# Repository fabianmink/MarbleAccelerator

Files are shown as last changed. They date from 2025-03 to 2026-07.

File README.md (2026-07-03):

# Marble Accelerator
This project deals with the construction of various accelerators (coil guns) for metallic marbles. It might be used e.g. for the GraviTrax marble run (marble data: $m = 8.6 \mathrm{g}$, $d = 12.7 \mathrm{mm}$). It has been used in various student projects in electrical engineering bachelor's and master's programs in the IEM department at the THM Friedberg, e.g. [this one](https://www.youtube.com/watch?v=bSArWLXCZdo) 

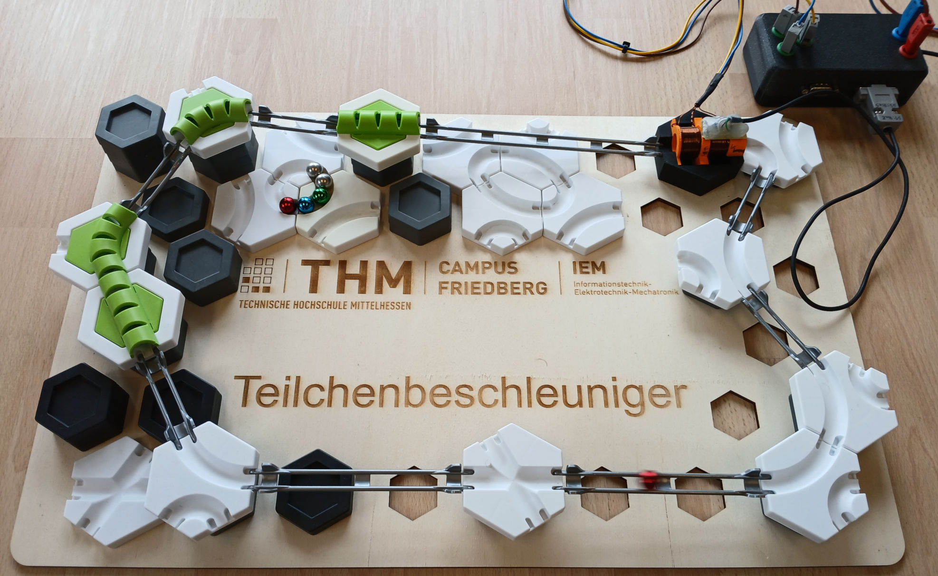
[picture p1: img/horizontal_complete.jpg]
Horizontal design complete
 

## Coilgun Designs

Coil winding cross sections are 15mm (coil length) x 7mm (inner radius 8mm, outer radius 15mm), leading to around 350 turns for 0.5mm wire diameter which results in an inductance of approximately 1mH.

### Horizontal coil design with two coils
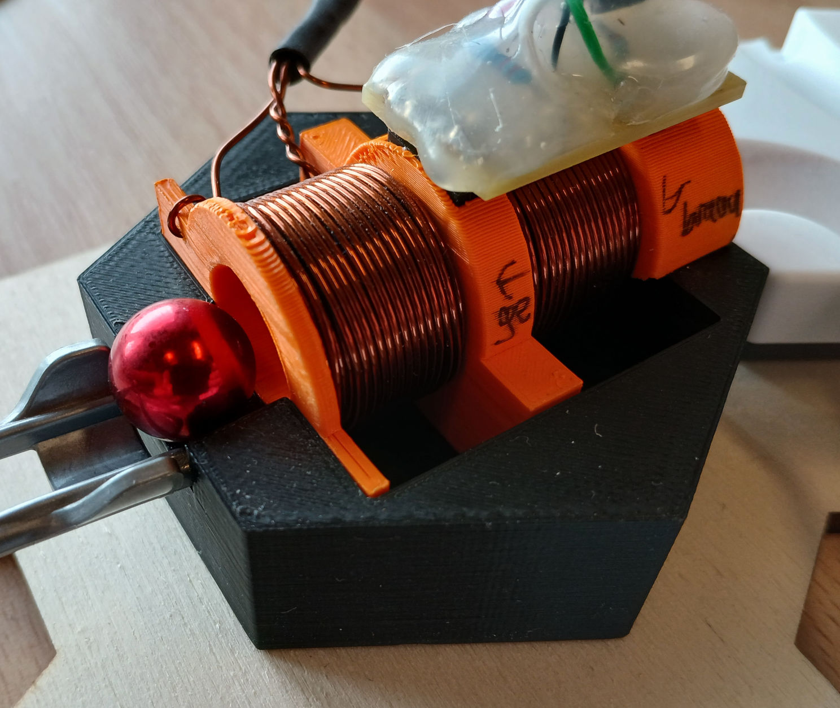
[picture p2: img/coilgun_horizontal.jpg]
Horizontal coil design


Horizontal CAD design (base and tube parts)

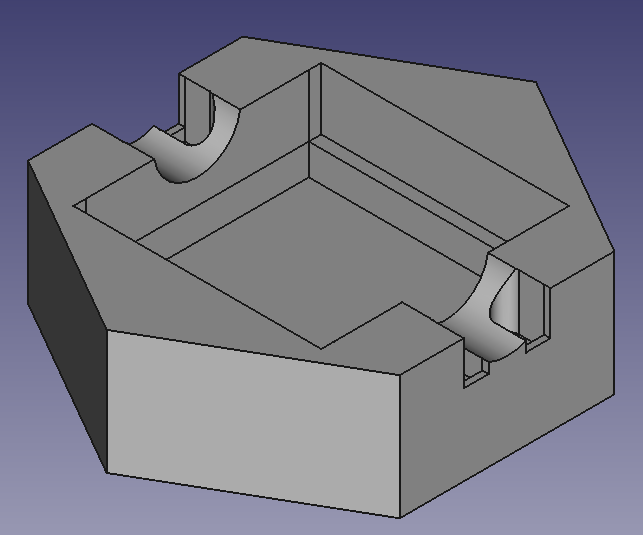
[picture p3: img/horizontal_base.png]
horizontal design base
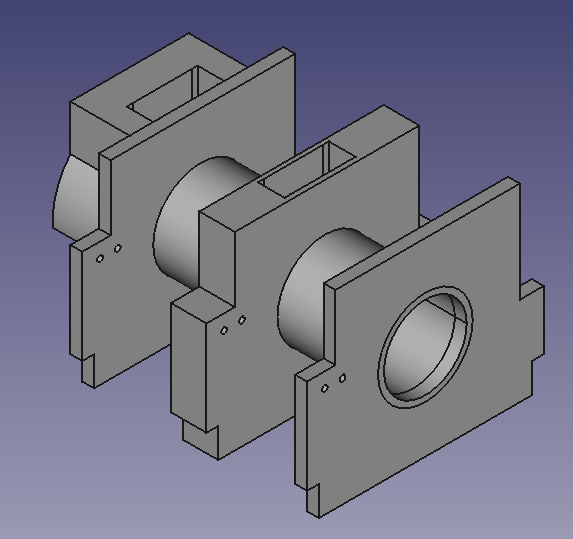
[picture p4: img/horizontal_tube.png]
horizontal design tube
 

The design is intended to be used with EVERLIGHT ITR9904 optical sensor for marble detection.

### Vertical coil design (single coil)

Vertical CAD design (base part and output)

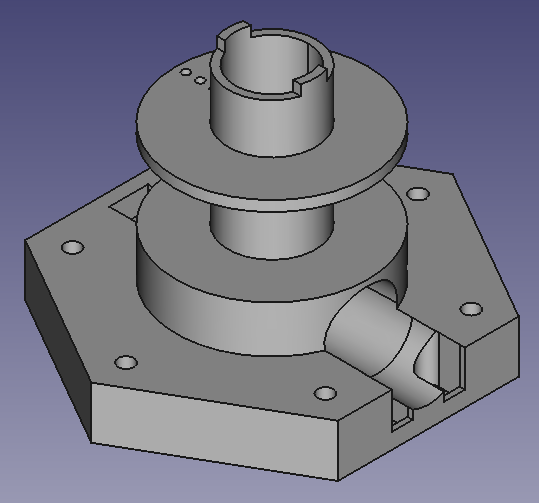
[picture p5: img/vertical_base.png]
vertical design base
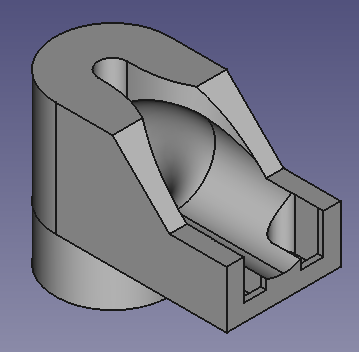
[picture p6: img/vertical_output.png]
vertical output
  

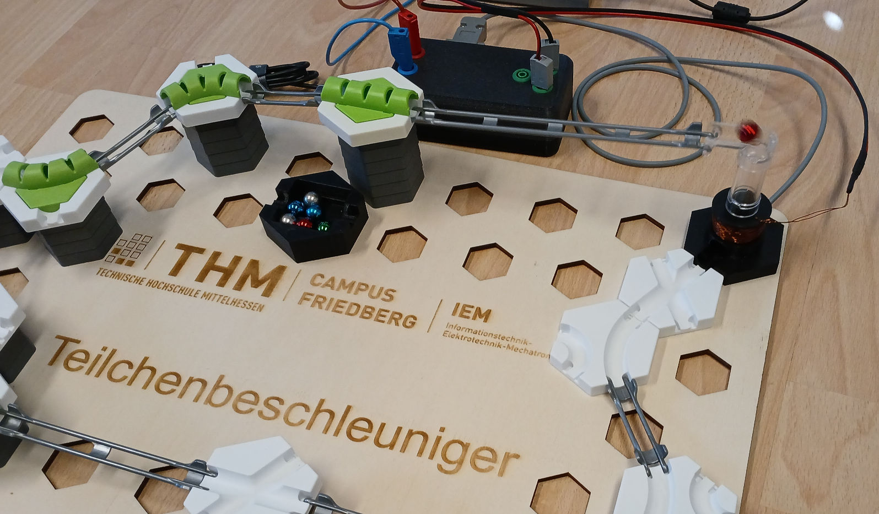
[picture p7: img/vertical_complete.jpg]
vertical whole marble track


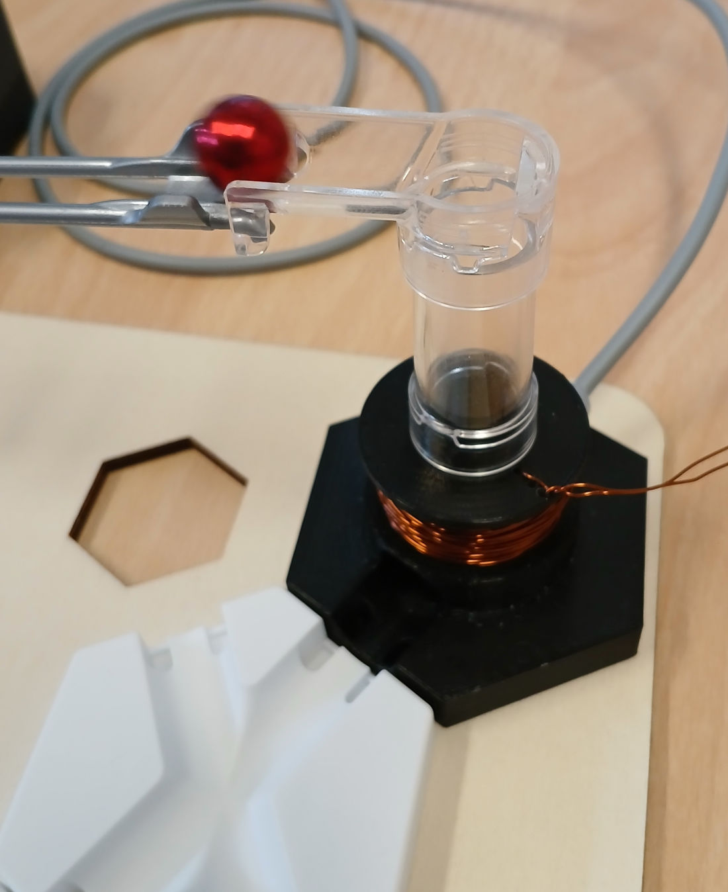
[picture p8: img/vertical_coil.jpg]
vertical design accelerator coil


The design is intended to be used with Vishay CNY70 optical sensor for marble detection.

The advantage of the vertical design is that the marble is at a defined state (no movement, $v_\mathrm{z} = 0$) at the beginning. This makes the accelerator parameters easier to tune, as the current level and duration of the current pulse are always the same.

## Coil winding
For an operating voltage of 24V, suitable wire diameters are in the range of 0.5mm ... 0.75mm.

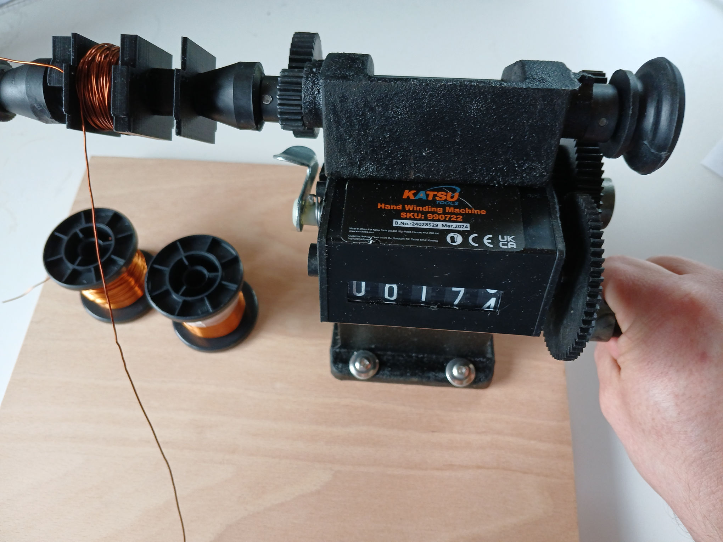
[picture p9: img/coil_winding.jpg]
coil winding machine


## FEM Simulation (FEMM)

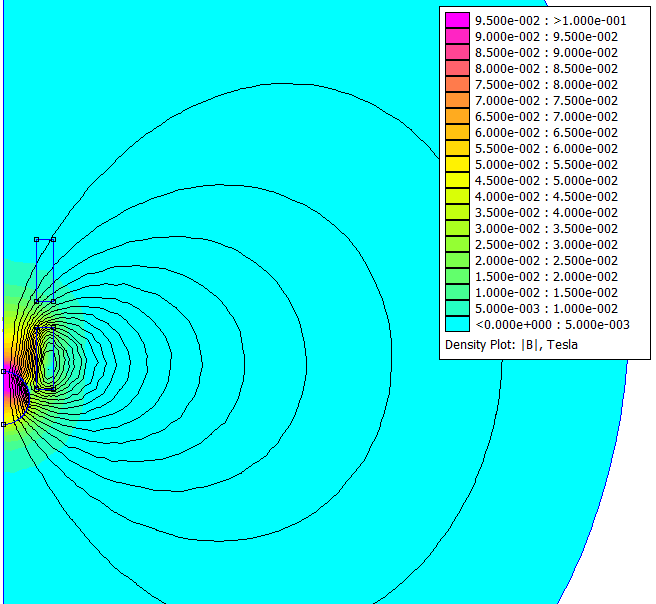
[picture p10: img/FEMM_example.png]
FEM Simulation


## Fitting of FEM results

The fit is based on the following coenergy equation:

- Co-Energy: $E_{\mathrm{Co}} = \frac{1}{2} \cdot L_\mathrm{min} \cdot I^2 \cdot \left[ 1 + d \cdot \exp \left( -0.5 \cdot \left(\frac{z - z_0}{z_\mathrm{s}}\right)^2 \right) \right]$

i.e.:

- z-Direction Force: $F_\mathrm{z} = \frac{\partial E_{\mathrm{Co}}}{\partial z} = - \frac{1}{2}  \cdot L_\mathrm{min} \cdot I^2 \cdot \left[ d \cdot \exp \left( -0.5 \cdot \left( \frac{z - z_0}{z_\mathrm{s}} \right)^2 \right) \right] \cdot \frac{z - z_0}{z^2_\mathrm{s}}$

- Flux Linkage: $\Psi = \frac{\partial E_{\mathrm{Co}}}{\partial I} = L_\mathrm{min} \cdot I \cdot \left[ 1 + d \cdot \exp \left( -0.5 \cdot \left( \frac{z - z_0}{z_\mathrm{s}} \right)^2 \right) \right]$

- Inductance: $L = \frac{\partial \Psi}{\partial I} = \frac{\partial^2 E_{\mathrm{Co}}}{\partial I^2} = L_\mathrm{min} \cdot \left[ 1 + d \cdot \exp \left( -0.5 \cdot \left( \frac{z - z_0}{z_\mathrm{s}} \right)^2 \right) \right]$

- Flux derivative: $\frac{\partial \Psi}{\partial z} = \frac{\partial^2 E_{\mathrm{Co}}}{\partial I \partial z} = - L_\mathrm{min} \cdot I \cdot \left[ d \cdot \exp \left( -0.5 \cdot \left( \frac{z - z_0}{z_\mathrm{s}} \right)^2 \right) \right] \cdot \frac{z - z_0}{z^2_\mathrm{s}}$ (needed for induced voltage calculation)

- Maximum force for given current occurs at the inflection points of $E_{\mathrm{Co}}$, i.e. at $z = z_0 \pm z_\mathrm{s}$: $F_\mathrm{z,max} \left( I \right)= \frac{1}{2}  \cdot L_\mathrm{min} \cdot I^2 \cdot d \cdot \exp \left( -0.5 \right) \cdot \frac{1}{z_\mathrm{s}}$

Resulting examplary fitted force:

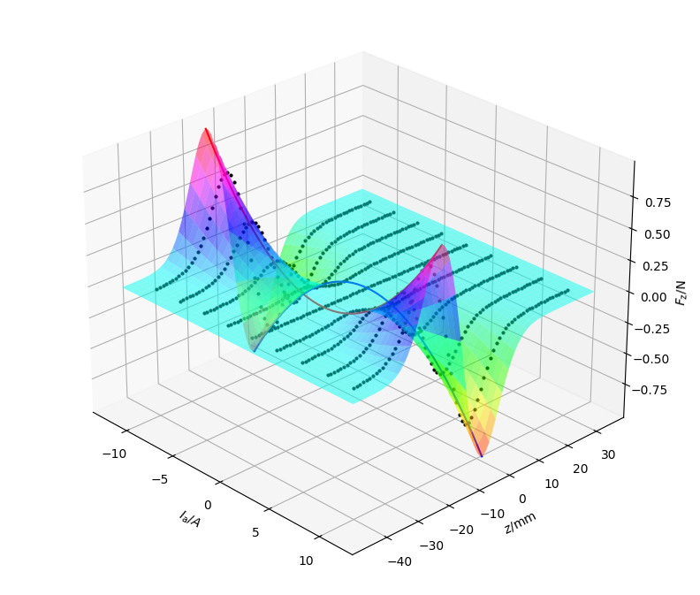
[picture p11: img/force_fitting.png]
Force Fit


## Dynamic System Simulation Model

The dynamic simulation implements the following equations:

- Velocity (z-direction): $\dot{v} = \frac{1}{m} \cdot F_\mathrm{z}$
- z-Position: $\dot{z} = v$
- Force calculation: $F_\mathrm{z} = F_\mathrm{z}\left(I, z\right)$ (see equation in chapter above)
- Coil current: $\dot{I} = \frac{1}{L \left(I, z\right) } \cdot \left[ u - R \cdot I - u_\mathrm{ind} \right]$
- Induced voltage: $u_\mathrm{ind} = \frac{\partial \Psi}{\partial z} \cdot v$

Model:

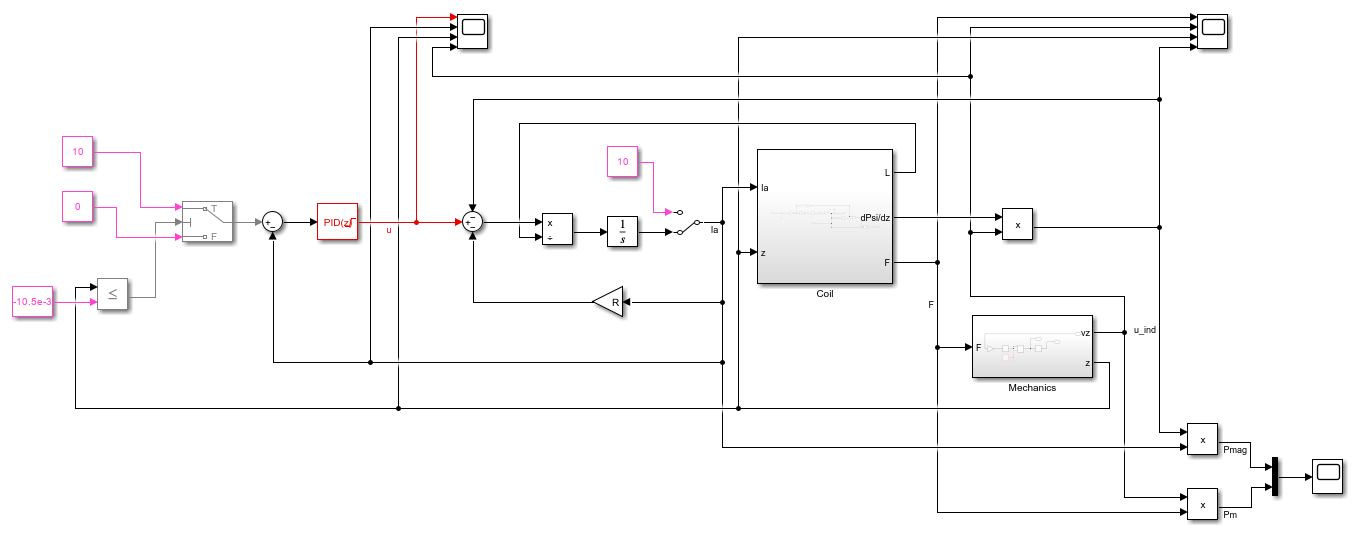
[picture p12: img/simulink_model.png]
System Simulation


Coil electromagnetic subsystem:

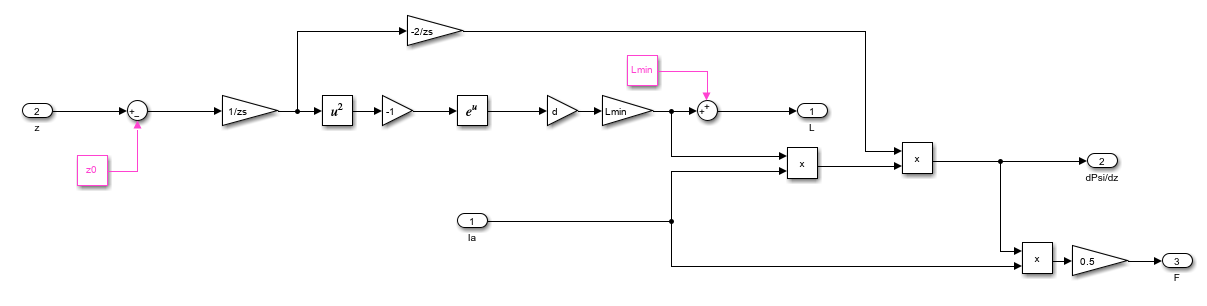
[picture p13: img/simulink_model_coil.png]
Model of coil electromagnetic system


## Power Electronics / Software

The software is designed for STM's B-G431B-ESC1 (Discovery kit with STM32G431CB MCU); it also includes the neccessary power MOSFETs. The supply voltage is 24V. An external capacitor of approximately 20mF is recommended in order to provide the high pulsed currents of 10..20A for durations of a few 10ms.

### Boost Converter

In case the coil should be battery-powered (e.g. from 3x AA alkaline cells / 4.5V), the boost converter board can be used.

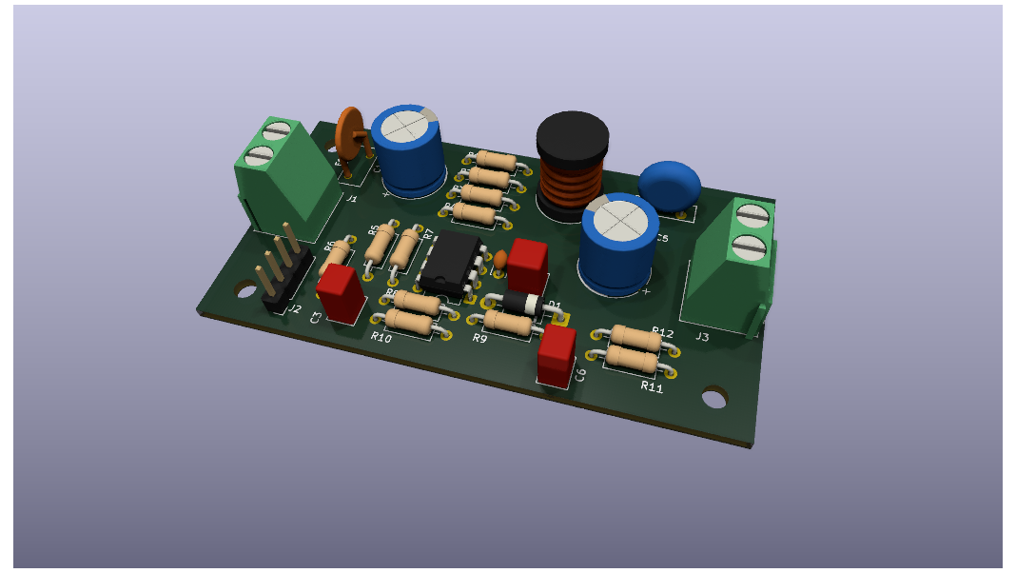
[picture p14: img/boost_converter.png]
Boost Converter Board


### Hi-Side Switch

Can be used to power the coil.

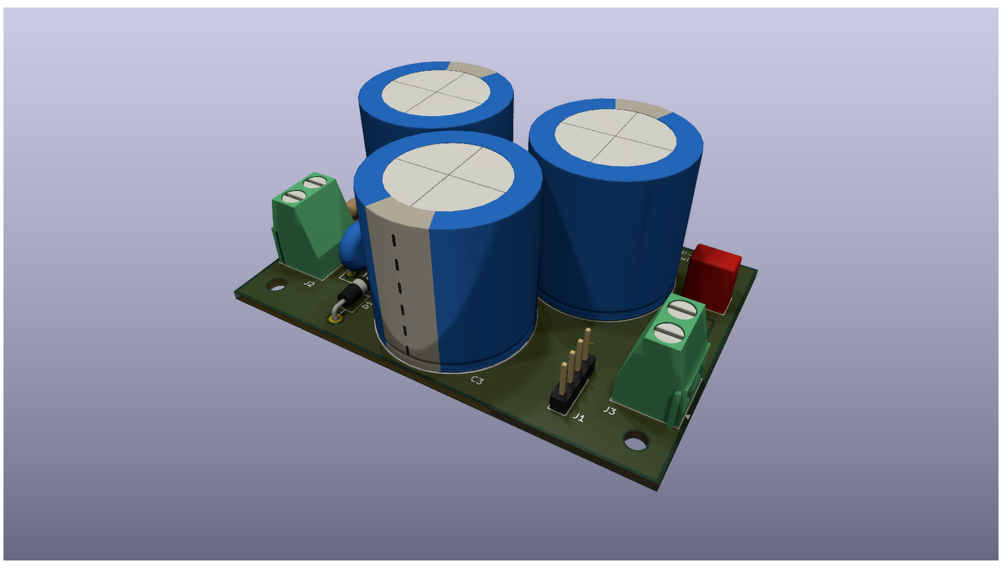
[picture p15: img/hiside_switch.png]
Hi-Side Switch Board


## Simlar projects

- [lincoln1clarke (Instructables) - Electromagnetic Marble Accelerator for Gravitrax](https://www.instructables.com/Electromagnetic-Marble-Accelerator-for-Gravitrax/)
- [HyperspacePirate (Thingiverse) - Electromagnetic Accelerator](https://www.thingiverse.com/thing:4918703)
- [William Le - Perpetual Marble Machine](https://lovelywings.store/)

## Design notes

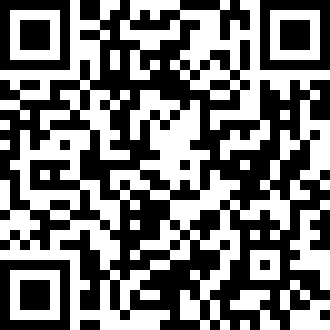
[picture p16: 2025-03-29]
img/MarbleAccelerator.png

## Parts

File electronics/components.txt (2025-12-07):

Input current limitation
Preferred Input voltage U = 3V / Ri = 0.3Ohm
(2x Alkaline)
https://de.wikipedia.org/wiki/Alkali-Mangan-Zelle
Gemessener Kurzschlussstrom (1x Aldi-Zelle AA): 7.5A (mit Messleitungen) -> Ri ~~ 0.15 .. 0.2 Ohm kommt hin
Eingangsstrom auf 1A begrenzen (PTC-Sicherung)
-> 3W
Bspw. Kosmos 3V-Batteriemodule 2xAA PTC "X30 UF110" vermutl. 30V, 1.1A (Reichelt "PTC FRU11030F" (Eska) ), begrenzen auf ca. 6A messtechnisch ermittelt (passt zu Datenblattangabe 50mOhm...170mOhm Innenwiderstand)
Denkbare Typen:
Reichelt PTC FRU09030F  (30V, 0.9A)
Reichelt PTC FRU11030F  (30V, 1.1A)
Reichelt PTC FRX05060F  (60V, 500mA)
Reichelt PTC FRX11060F  (60V, 1.1A)

Power Switches
BTS 6163 D Smart Highside Power Switch

Storage Capacitor
Cstor ≈ 20mF
e.g. 
2x Reichelt BSN 10.000/25     Becher-Elko, radial, 10 mF, 25 
1x Reichelt BSN 22.000/40     Becher-Elko, radial, 22 mF, 40 

PTC, for Charging Cstor
e.g.
Reichelt  EPC B59990-C80      Infineon PTC Widerstand, 55 Ohm, 80 V, 80°C 

DC-DC converter
MC34063A
1N5819
Rsc = 2W, ≈ 0.2Ohm
L ≈ 170uH
Cin = 100uF, low ESR
Cout = 330uF, low ESR

Reflective Optical Sensor
CNY 70
ELI TR9904

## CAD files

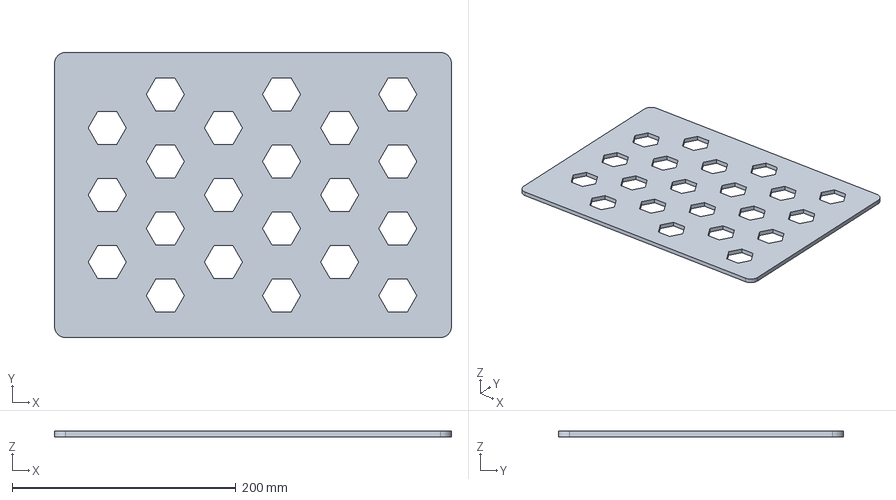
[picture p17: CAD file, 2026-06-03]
cad/Baseplate_35cmx25cm_variableCell.FCStd
355.0 x 255.0 x 5.00 mm

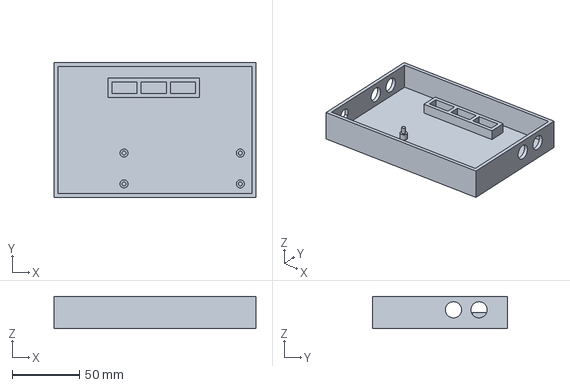
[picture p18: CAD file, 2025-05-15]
cad/controller/baseplate.FCStd
150.0 x 100.0 x 24.0 mm

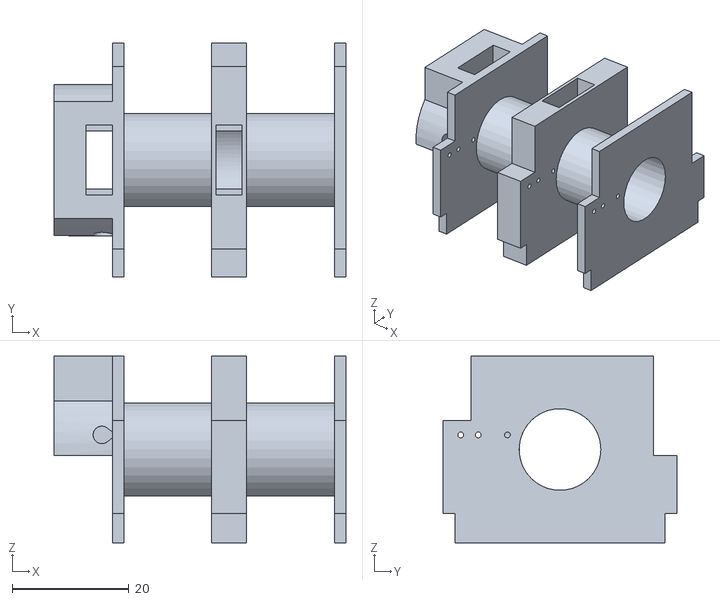
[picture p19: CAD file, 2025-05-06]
cad/horizontal/tube-Body.stl
50.0 x 40.0 x 32.0

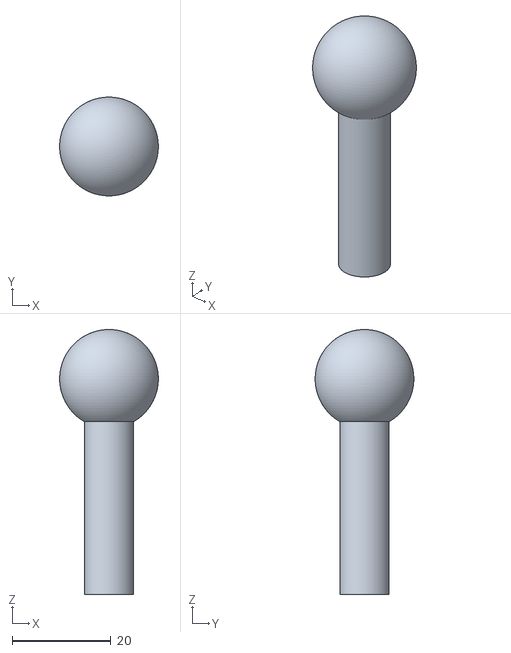
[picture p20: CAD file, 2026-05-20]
cad/magnet/magnetHolder-Body.stl
20.0 x 20.0 x 53.7

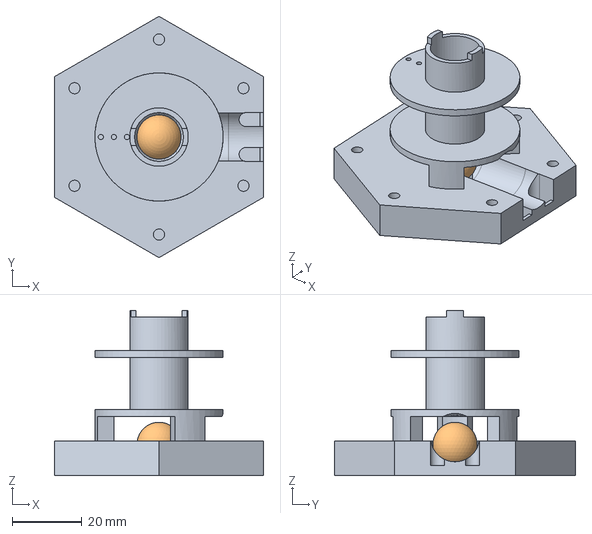
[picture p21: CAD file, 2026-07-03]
cad/vertical/base_open.FCStd
60.0 x 69.3 x 47.5 mm
Marble

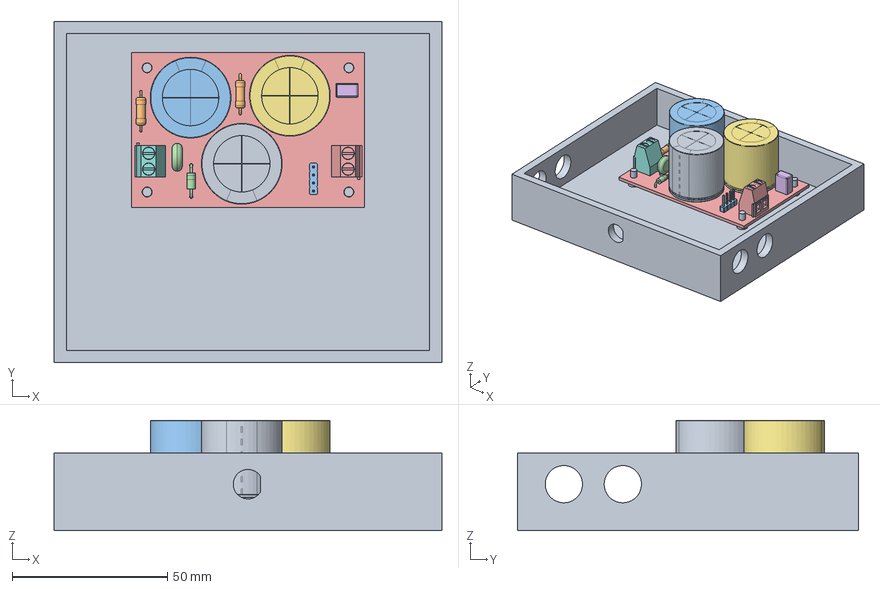
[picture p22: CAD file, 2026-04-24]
electronics/housing/board_carrier_SwitchOnly.FCStd
125.0 x 110.0 x 35.6 mm
BoardCarrier
R_Axial_DIN0309_L9.0mm_D3.2mm_P12.70mm_Horizontal
PinHeader_1x04_P2.54mm_Vertical
D_DO-41_SOD81_P10.16mm_Horizontal
TerminalBlock_Phoenix_MKDS-1,5-2-5.08_1x02_P5.08mm_Horizontal
C_Rect_L7.2mm_W4.5mm_P5.00mm_FKS2_FKP2_MKS2_MKP2
CP_Radial_D26.0mm_P10.00mm_SnapIn
TerminalBlock_Phoenix_MKDS-1,5-2-5.08_1x02_P5.08mm_Horizontal001
CP_Radial_D26.0mm_P10.00mm_SnapIn001
R_Axial_DIN0309_L9.0mm_D3.2mm_P12.70mm_Horizontal001
CP_Radial_D26.0mm_P10.00mm_SnapIn002
RV_Disc_D9mm_W3.3mm_P5mm
R_0805_2012Metric
C_0805_2012Metric
R_0805_2012Metric001
R_0805_2012Metric002
C_0805_2012Metric001
SOT-23
R_0805_2012Metric003
hiside_switch 1.19.1
hiside_switch 1.19.002
hiside_switch 1.19.003
hiside_switch 1.19.004
hiside_switch 1.19.005
hiside_switch 1.19.006
hiside_switch 1.19.007
R_0805_2012Metric004
R_0805_2012Metric005
hiside_switch_PCB

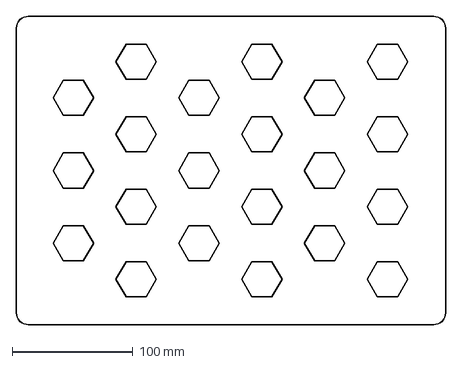
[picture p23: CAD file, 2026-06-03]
cad/Baseplate_35cmx25cm-BodySketch_Baseplate.dxf
355.0 x 255.0 mm

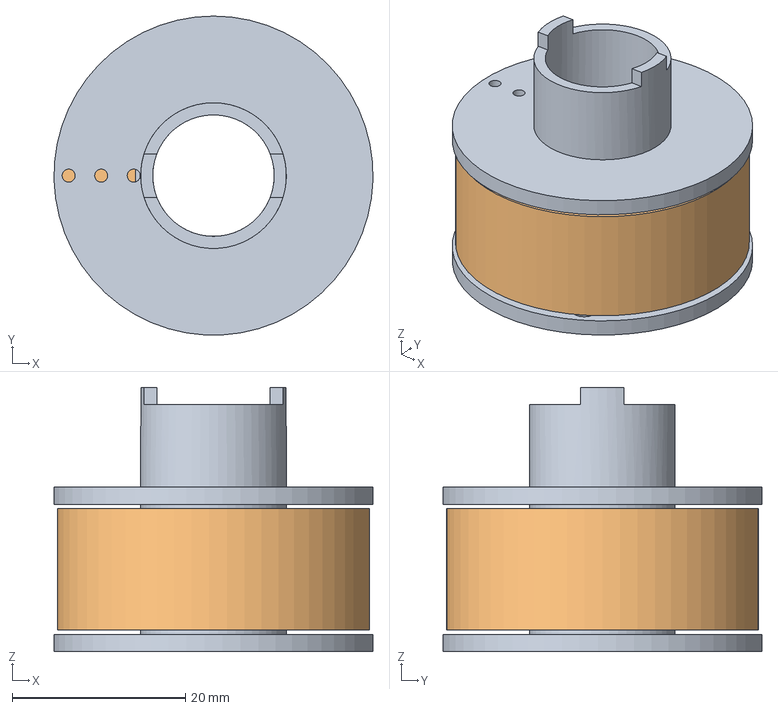
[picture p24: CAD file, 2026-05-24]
cad/vertical/base_open_coil.FCStd
36.8 x 36.8 x 30.5 mm
Body_Winding

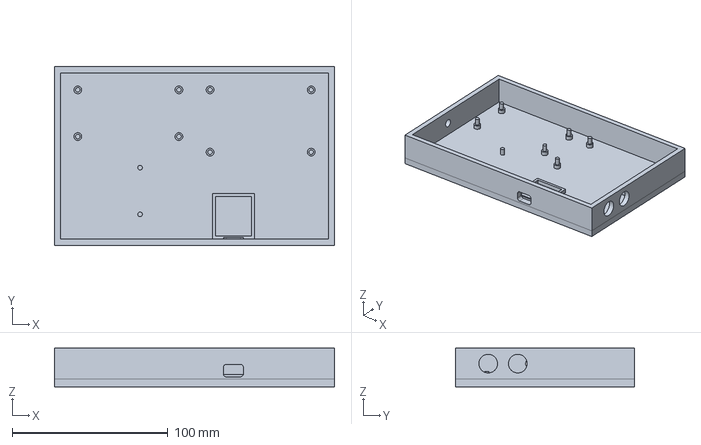
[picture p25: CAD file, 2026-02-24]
electronics/housing/board_carrier.FCStd
180.0 x 115.0 x 25.0 mm

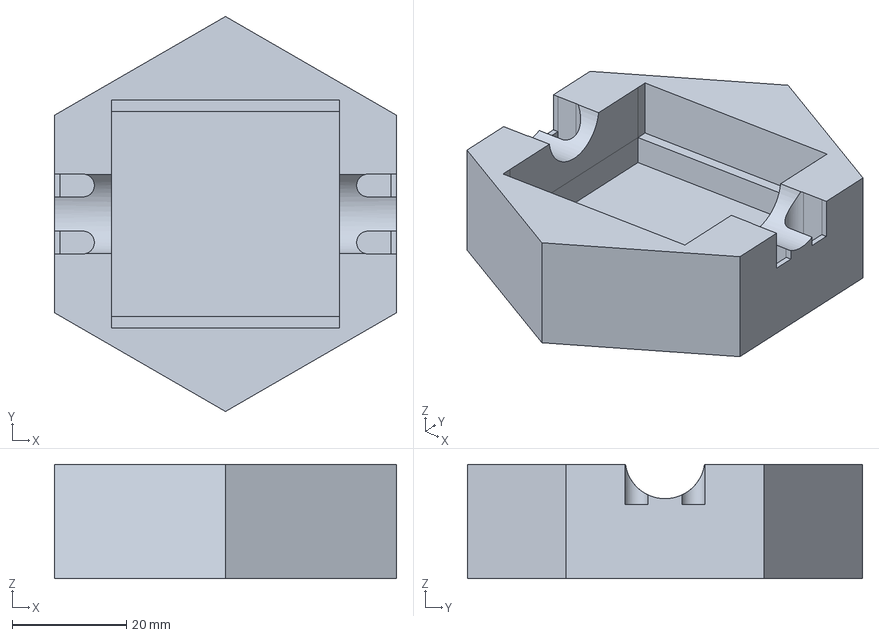
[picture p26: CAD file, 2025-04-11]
cad/horizontal/base.FCStd
60.0 x 69.3 x 20.0 mm

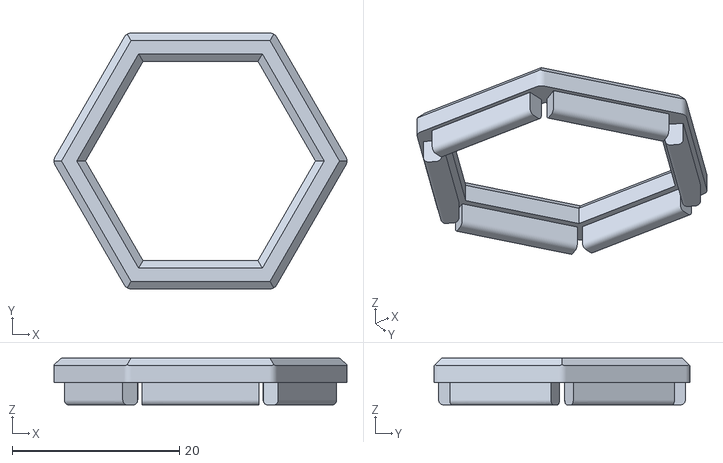
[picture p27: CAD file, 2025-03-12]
cad/ring.stl
35.0 x 30.6 x 5.60

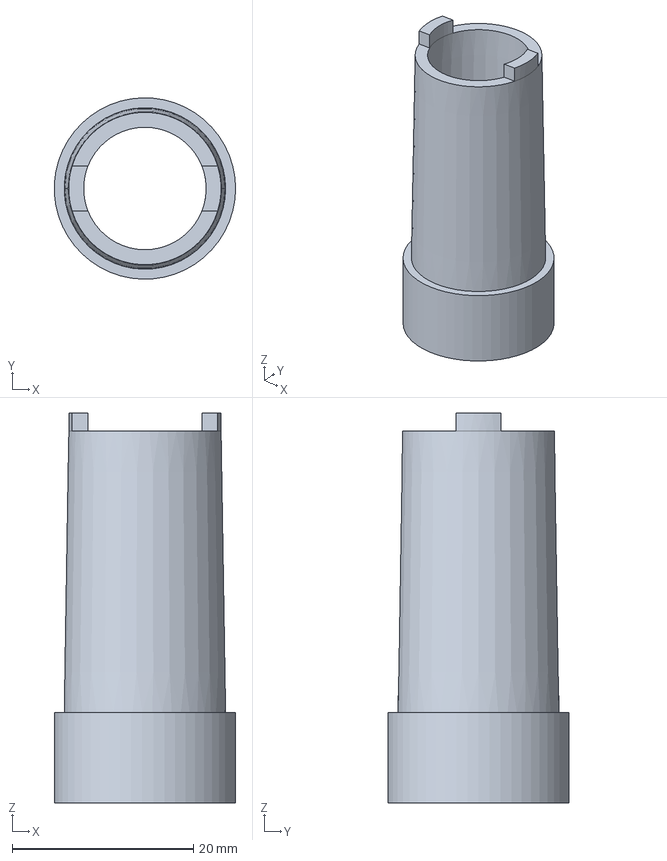
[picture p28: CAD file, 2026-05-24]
cad/vertical/extensionTube.FCStd
20.0 x 20.0 x 43.0 mm

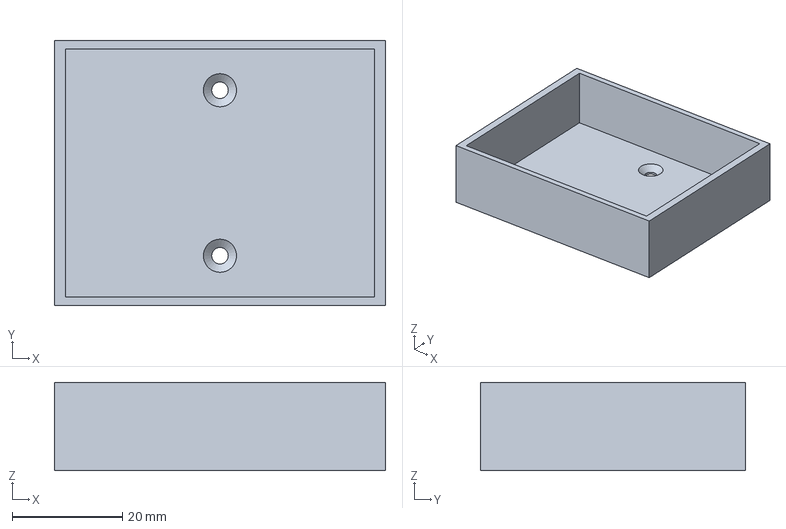
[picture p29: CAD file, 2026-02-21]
electronics/housing/batteryHolder.FCStd
60.0 x 48.0 x 16.0 mm

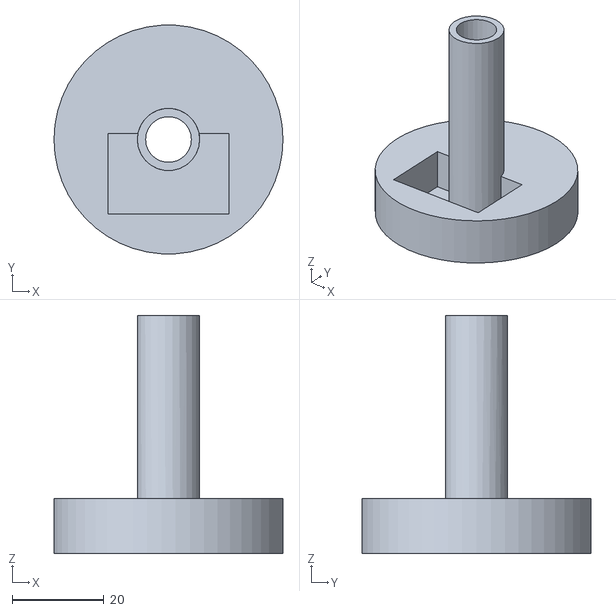
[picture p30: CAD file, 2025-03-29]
cad/horizontal/winding_assistant-Body.stl
50.0 x 49.9 x 52.0

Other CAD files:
electronics/housing/electronicsAssembly.FCStd
cad/controller/baseplate-Body.stl
cad/horizontal/tube.FCStd
cad/magnet/magnetHolder.FCStd
cad/horizontal/base-Body.stl
cad/horizontal/winding_assistant.FCStd
cad/vertical/Pin-Body.stl
cad/vertical/Pin.FCStd
cad/vertical/base-Body.stl
cad/vertical/base.FCStd
cad/vertical/base_open-Body.stl
cad/vertical/base_open_base-Body.stl
cad/vertical/base_open_base.FCStd
cad/vertical/base_open_coil-Body.stl
cad/vertical/base_open_coil_noTop-Body.stl
cad/vertical/base_open_coil_noTop.FCStd
cad/vertical/extensionTube-Body.stl
cad/vertical/extensionTube_70mm-Body.stl
cad/vertical/outputCatcher-Body.stl
cad/vertical/outputCatcher.FCStd
cad/vertical/outputCatcherFilled-Body_Catcher.stl
cad/vertical/outputCatcherFilled-Body_Plate.stl
cad/vertical/outputCatcherFilled.FCStd
cad/vertical/outputTube-Body.stl
cad/vertical/outputTube.FCStd
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

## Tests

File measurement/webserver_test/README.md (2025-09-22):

# Webserver-Test

This is test application framework for displaying measurements on a webpage using uvicorn webserver / plotly. Code was partly developed in CaseStudy Project in Summer 2025.

Currently, it does not work together with the accelerator firmware for the STM32 controller of this project.

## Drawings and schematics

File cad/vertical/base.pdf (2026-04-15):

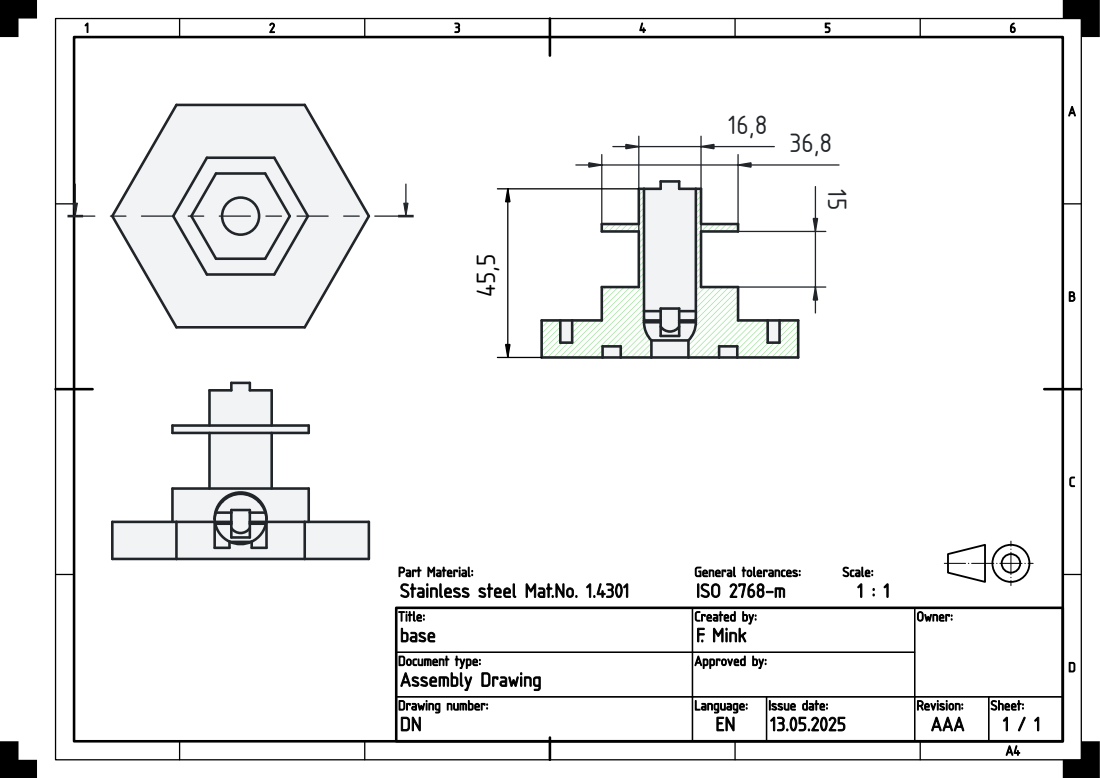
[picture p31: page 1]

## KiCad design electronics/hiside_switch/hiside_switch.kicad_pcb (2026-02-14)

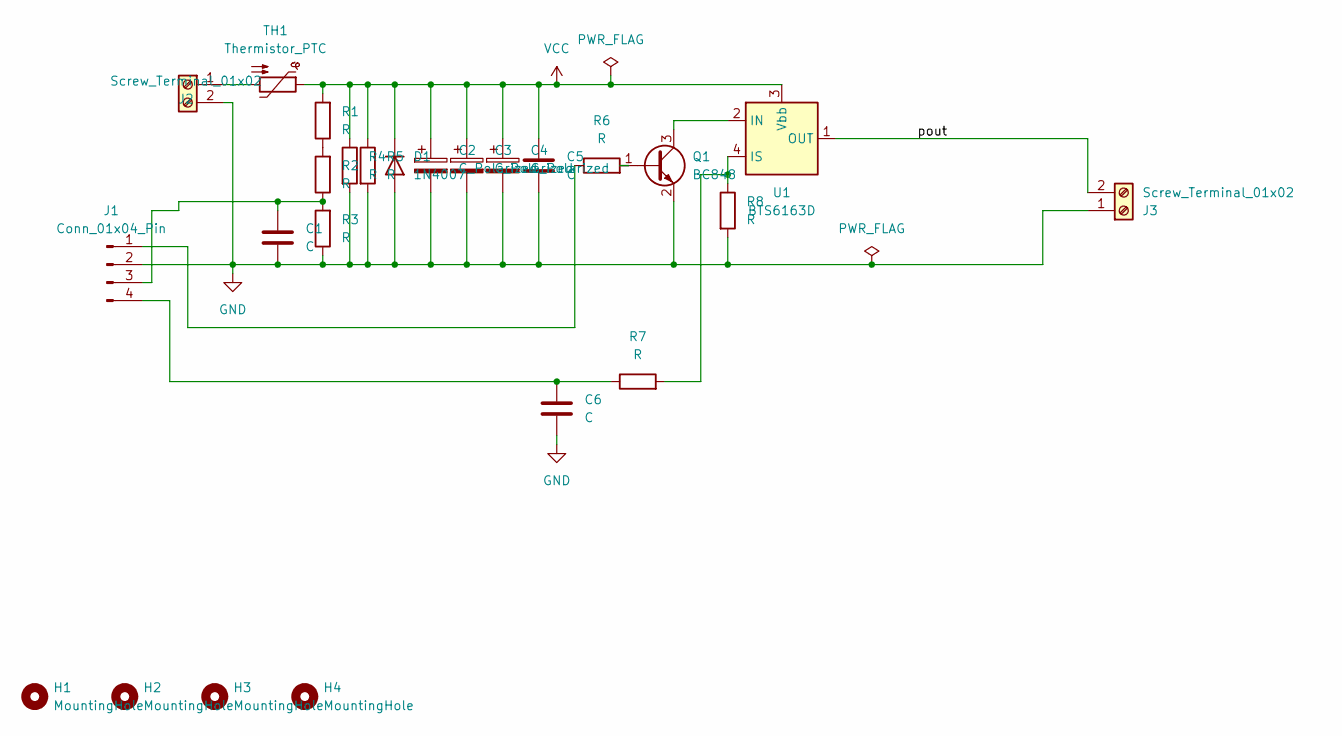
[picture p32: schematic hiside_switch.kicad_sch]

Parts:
C1, C6: C; C_0805_2012Metric_Pad1.18x1.45mm_HandSolder
C2, C3, C4: C_Polarized; CP_Radial_D26.0mm_P10.00mm_SnapIn
C5: C; C_Rect_L7.2mm_W4.5mm_P5.00mm_FKS2_FKP2_MKS2_MKP2
D1: 1N4007; D_DO-41_SOD81_P10.16mm_Horizontal
H1, H2, H3, H4: MountingHole; MountingHole_3.2mm_M3
J1: Conn_01x04_Pin; PinHeader_1x04_P2.54mm_Vertical
J2, J3: Screw_Terminal_01x02; TerminalBlock_Phoenix_MKDS-1,5-2-5.08_1x02_P5.08mm_Horizont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
Q1: BC848; SOT-23
R1, R2, R3, R6, R7, R8: R; R_0805_2012Metric_Pad1.20x1.40mm_HandSolder
R4, R5: R; R_Axial_DIN0309_L9.0mm_D3.2mm_P12.70mm_Horizontal
TH1: Thermistor_PTC; RV_Disc_D9mm_W3.3mm_P5mm
U1: BTS6163D; TO-252-4

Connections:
/pout: J3.2, U1.1 (OUT), U1.5 (OUT)
GND: C1.2, C2.2, C3.2, C4.2, C5.2, C6.2, D1.2 (A), J1.2, J2.2, J3.1, Q1.2 (E), R3.1, R4.2, R5.2, R8.2
unnamed: J1.1, R6.1
unnamed: C1.1, J1.3, R2.1, R3.2
unnamed: C6.1, J1.4, R7.1
unnamed: J2.1, TH1.2
unnamed: Q1.1 (B), R6.2
unnamed: Q1.3 (C), U1.2 (IN)
unnamed: R1.1, R2.2
unnamed: R7.2, R8.1, U1.4 (IS)
VCC: C2.1, C3.1, C4.1, C5.1, D1.1 (K), R1.2, R4.1, R5.1, TH1.1, U1.3 (Vbb)

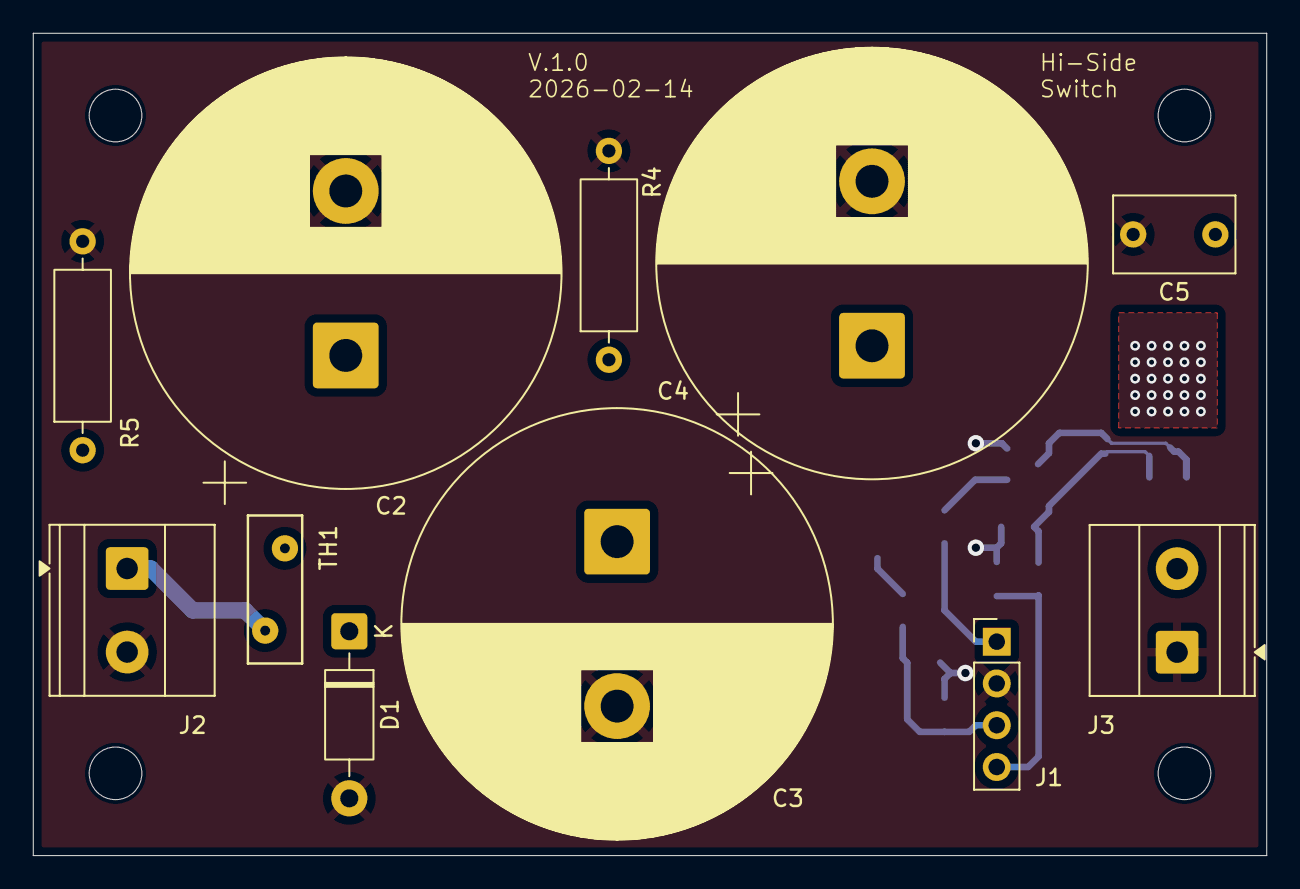
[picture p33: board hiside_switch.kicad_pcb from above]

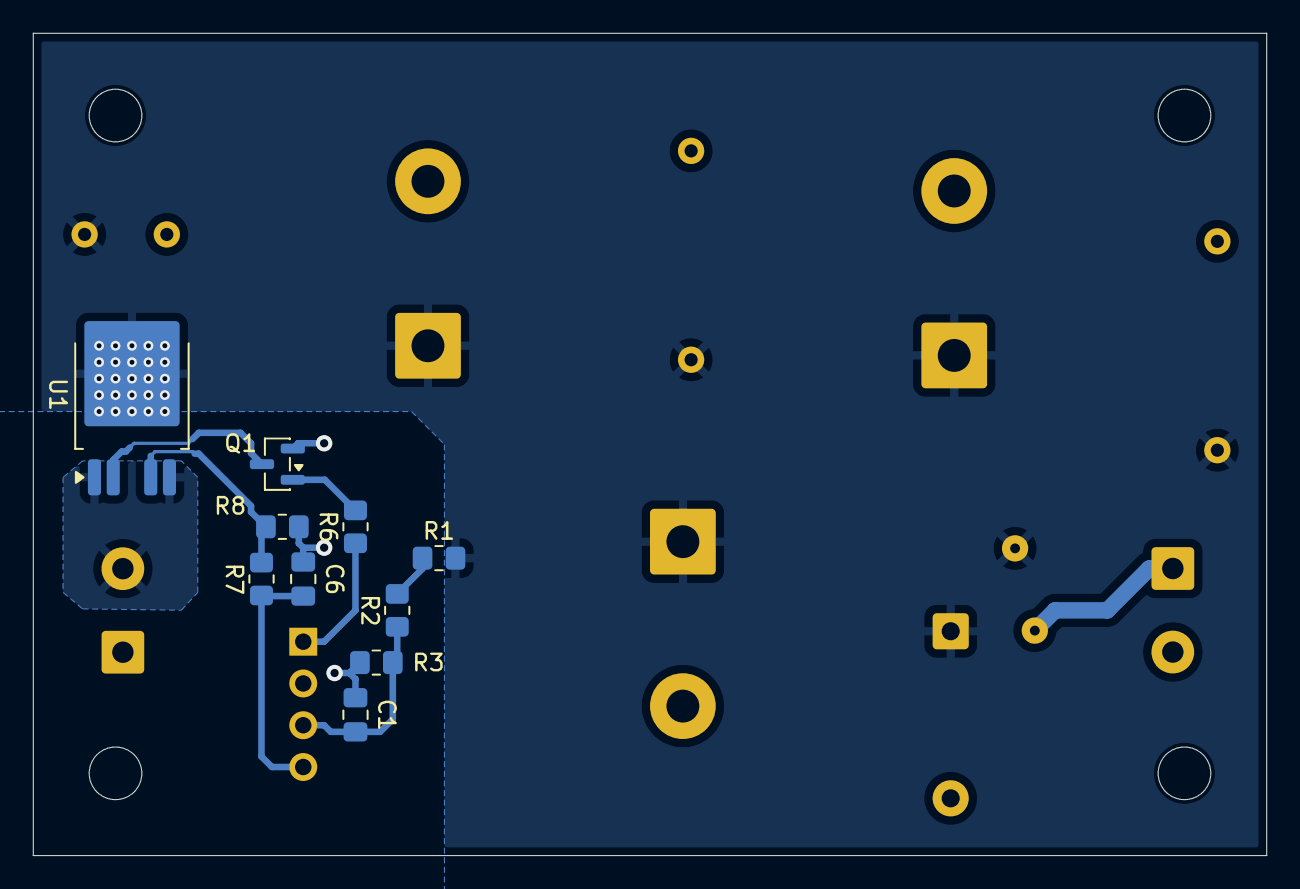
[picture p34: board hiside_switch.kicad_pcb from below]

Board: 2 copper layers, 75.0 x 50.0 mm, 25 parts (10 on the bottom side), 11 nets.

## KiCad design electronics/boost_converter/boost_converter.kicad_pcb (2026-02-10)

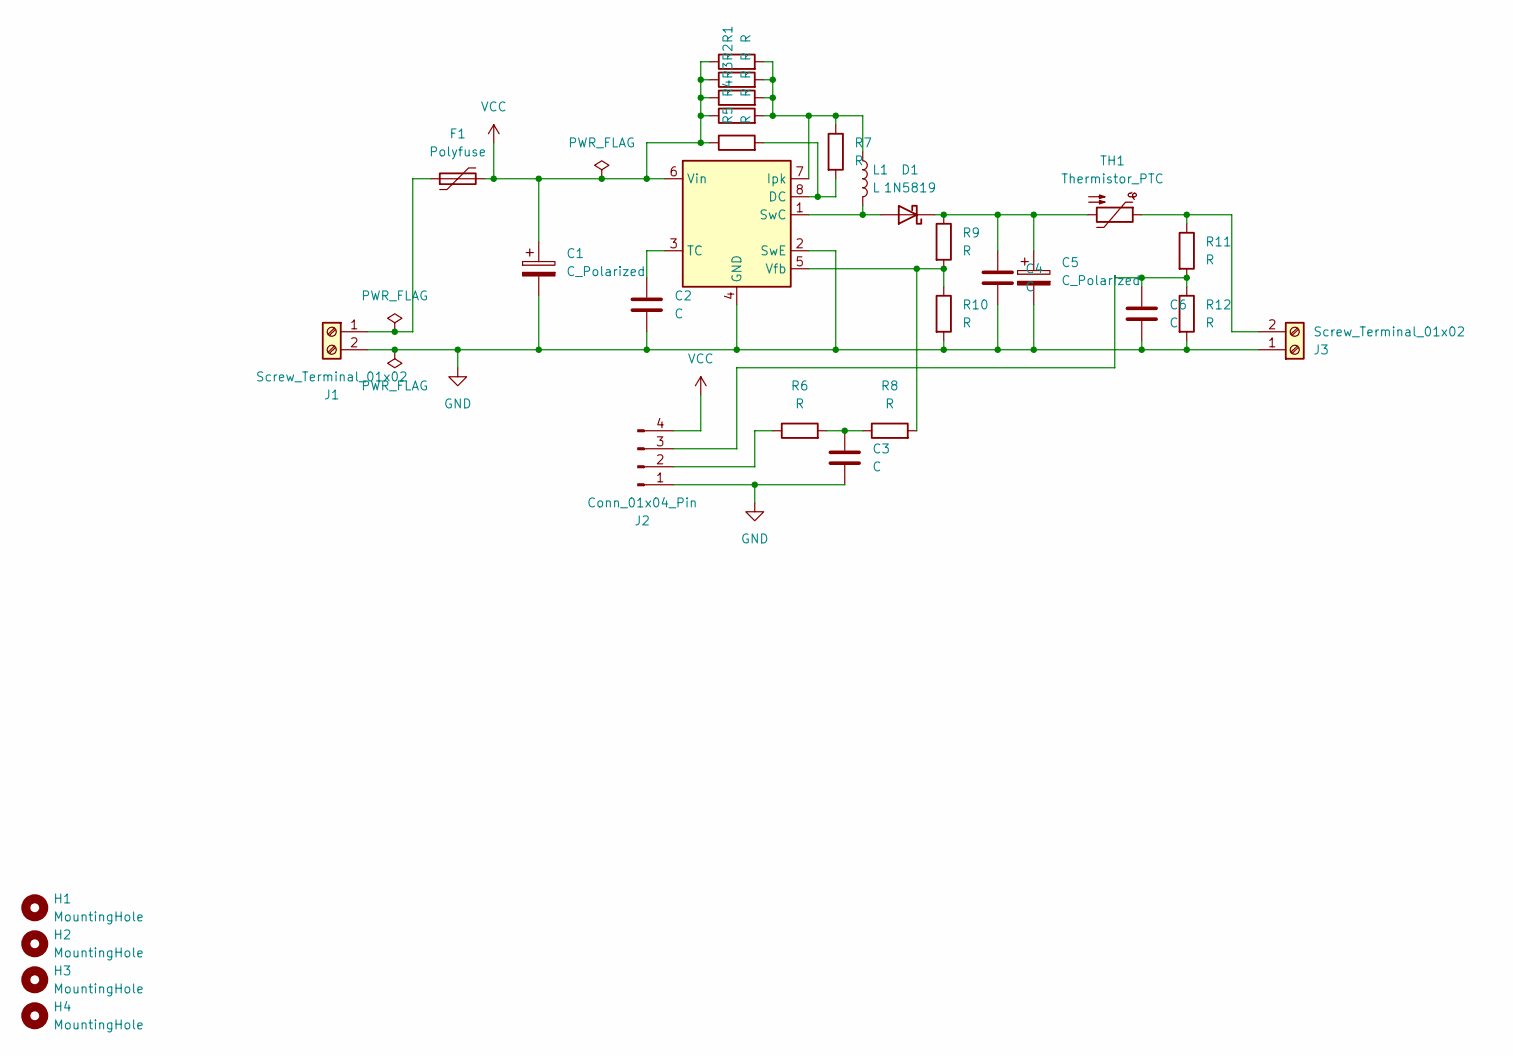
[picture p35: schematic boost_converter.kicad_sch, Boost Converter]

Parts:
C1: C_Polarized; CP_Radial_D10.0mm_P2.50mm_P5.00mm
C2: C; C_Disc_D3.0mm_W2.0mm_P2.50mm
C3, C6: C; C_Rect_L4.6mm_W3.8mm_P2.50mm_MKS02_FKP02
C4: C; C_Rect_L4.6mm_W4.6mm_P2.50mm_MKS02_FKP02
C5: C_Polarized; CP_Radial_D10.0mm_P5.00mm_P7.50mm
D1: 1N5819; D_DO-41_SOD81_P10.16mm_Horizontal
F1: Polyfuse; Fuse_BelFuse_0ZRE0005FF_L8.3mm_W3.8mm
H1, H2, H3, H4: MountingHole; MountingHole_3.2mm_M3
J1, J3: Screw_Terminal_01x02; TerminalBlock_Phoenix_MKDS-1,5-2-5.08_1x02_P5.08mm_Horizont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
J2: Conn_01x04_Pin; PinHeader_1x04_P2.54mm_Vertical
L1: L; L_Radial_D10.0mm_P5.00mm_Fastron_07P
R1, R2, R3, R4, R5, R6, R7, R8, R9, R10, R11, R12: R; R_Axial_DIN0207_L6.3mm_D2.5mm_P10.16mm_Horizontal
TH1: Thermistor_PTC; RV_Disc_D9mm_W3.3mm_P5mm
U1: MC34063AP; DIP-8_W7.62mm

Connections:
GND: C1.2, C2.2, C3.2, C4.2, C5.2, C6.2, J1.2, J2.1, J3.1, R10.2, R12.2, U1.2 (SwE), U1.4 (GND)
unnamed: C3.1, R6.2, R8.1
unnamed: D1.2 (A), L1.2, U1.1 (SwC)
unnamed: C4.1, C5.1, D1.1 (K), R9.1, TH1.2
unnamed: F1.1, J1.1
unnamed: J2.2, R6.1
unnamed: C6.1, J2.3, R11.2, R12.1
unnamed: J3.2, R11.1, TH1.1
unnamed: R5.2, R7.2, U1.8 (DC)
unnamed: L1.1, R1.2, R2.2, R3.2, R4.2, R7.1, U1.7 (Ipk)
unnamed: C2.1, U1.3 (TC)
unnamed: R8.2, R9.2, R10.1, U1.5 (Vfb)
VCC: C1.1, F1.2, J2.4, R1.1, R2.1, R3.1, R4.1, R5.1, U1.6 (Vin)

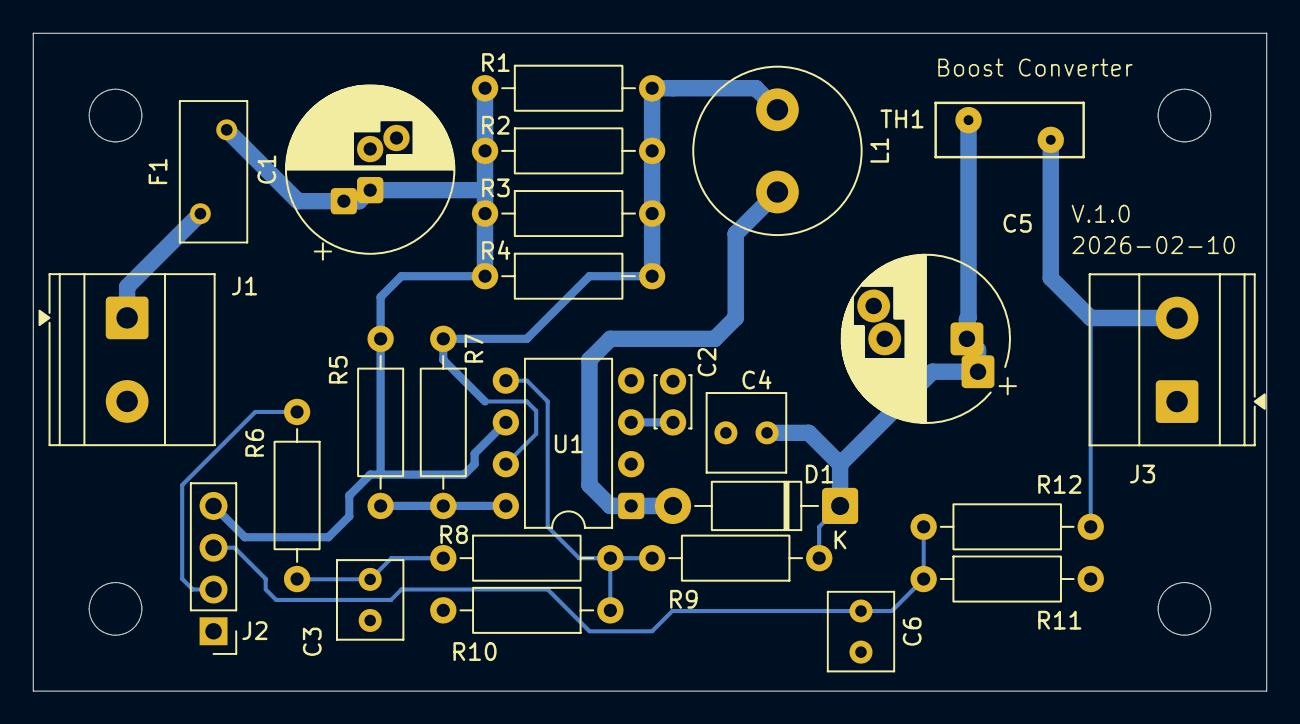
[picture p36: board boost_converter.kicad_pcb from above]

Board: 2 copper layers, 75.0 x 40.0 mm, 30 parts (0 on the bottom side), 13 nets.

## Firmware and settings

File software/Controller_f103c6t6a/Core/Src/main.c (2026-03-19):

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
/* Includes ------------------------------------------------------------------*/
#include "main.h"

/* USER CODE BEGIN Includes */
#include <stdint.h>
#include <string.h>
#include <stdlib.h>
/* USER CODE END Includes */


UART_HandleTypeDef huart1;

/* USER CODE BEGIN PV */
pulse_t pulse_data;
control_t control_data;
/* USER CODE END PV */

void SystemClock_Config(void);
static void MX_GPIO_Init(void);
static void MX_USART1_UART_Init(void);
static void MX_TIM3_Init(void);
static void MX_ADC1_Init(void);
/* USER CODE BEGIN 0 */
static void uart_print(UART_HandleTypeDef *huart, uint8_t *pData, uint16_t Size){
	HAL_UART_Transmit_IT(huart, pData, Size);
	//Wait until complete, as HAL_UART_Transmit_IT doesn't seem to copy the pData contents
	while(   HAL_UART_GetState(huart) != HAL_UART_STATE_READY ){
	}
}


static void uart_printstr(UART_HandleTypeDef *huart, char *str){
	size_t len;
	len = strlen(str);
	uart_print(huart, (uint8_t*)str, len);
}


void main_ctrl(void){

	//*** Generate output pulse ***
	if(pulse_data.state==ssi_state_idle){
		if(pulse_data.start){
			pulse_data.remain = pulse_data.len;
			pulse_data.state=ssi_state_run;
		}

	}
	else if(pulse_data.state==ssi_state_run){
		if(pulse_data.remain > 3200){
			LL_TIM_OC_SetCompareCH1(TIM3, 3201);
			pulse_data.remain -= 3200;
		}
		else {
			LL_TIM_OC_SetCompareCH1(TIM3, pulse_data.remain);
			pulse_data.remain = 0;
			pulse_data.state=ssi_state_ready;
		}
	}
	else if(pulse_data.state==ssi_state_ready){
		LL_TIM_OC_SetCompareCH1(TIM3, 0);
		pulse_data.start = 0;
		pulse_data.state = ssi_state_idle;
	}

	// *** Set v_Ref PWM duty cycle ***
	LL_TIM_OC_SetCompareCH2(TIM3, control_data.pwm_vref);

	uint16_t adc_timeout = 0;
	//currently no regular conversion used
	//regular conversion is only enabled because injected conversion is auto-triggered
	//at end of regular conversions
	//while(!LL_ADC_IsActiveFlag_EOS(ADC1)){
	//	//Error after certain time, if adc will not get ready!, stop PWM!
	//	if (adc_timeout >= 10) {
	//		//ERROR!!
	//	}
	//	else {
	//		adc_timeout++;
	//	}
	//}
	//get ADC value and switch to next channel
	//if(control_data.adc_ch == 0){
	//	value = (int16_t) LL_ADC_REG_ReadConversionData12(ADC1);
	//	LL_ADC_REG_SetSequencerRanks(ADC1, LL_ADC_REG_RANK_1, LL_ADC_CHANNEL_2);
	//	control_data.adc_ch = 1;
	//}
	//else {
	//	value = (int16_t) LL_ADC_REG_ReadConversionData12(ADC1);
	//	LL_ADC_REG_SetSequencerRanks(ADC1, LL_ADC_REG_RANK_1, LL_ADC_CHANNEL_1);
	//	control_data.adc_ch = 0;
	//}

	while(!LL_ADC_IsActiveFlag_JEOS(ADC1)){
		//Error after certain time, if adc will not get ready!, stop PWM!
		if (adc_timeout >= 10) {
			//ERROR!!
		}
		else {
			adc_timeout++;
		}
	}
	control_data.adc_data_v0 = (int16_t) LL_ADC_INJ_ReadConversionData12(ADC1, LL_ADC_INJ_RANK_1);
	control_data.adc_data_v1 = (int16_t) LL_ADC_INJ_ReadConversionData12(ADC1, LL_ADC_INJ_RANK_2);
}


/* USER CODE END 0 */

/**
  * @brief  The application entry point.
  * @retval int
  */
int main(void)
{

  /* MCU Configuration--------------------------------------------------------*/

  /* Reset of all peripherals, Initializes the Flash interface and the Systick. */
  HAL_Init();

  /* Configure the system clock */
  SystemClock_Config();

  /* Initialize all configured peripherals */
  MX_GPIO_Init();
  MX_USART1_UART_Init();
  MX_TIM3_Init();
  MX_ADC1_Init();
  /* USER CODE BEGIN 2 */

  uart_printstr(&huart1, "Marble Accelerator Interface\r\n");
  uart_printstr(&huart1, "MT-Labor, IEM, THM 2026\r\n");
  //int encpos = -100;

  pulse_data.state = ssi_state_idle;

  control_data.vCapRef = 24.5f;  //V
  control_data.vCapTol = 0.5f;   //V
  control_data.pulseLen = 10.0f; //ms
  control_data.pulseRep = 10.0f;  //s
  control_data.voltok = 2.0f;     //s
  control_data.active = 1;

  LL_ADC_Enable(ADC1);
  LL_ADC_REG_StartConversionExtTrig(ADC1, LL_ADC_REG_TRIG_EXT_RISING);


  LL_TIM_EnableCounter(TIM3);
  LL_TIM_CC_EnableChannel(TIM3, LL_TIM_CHANNEL_CH1);
  LL_TIM_CC_EnableChannel(TIM3, LL_TIM_CHANNEL_CH2);
  LL_TIM_EnableIT_UPDATE(TIM3);

  /* USER CODE END 2 */

  /* Infinite loop */
  /* USER CODE BEGIN WHILE */
  while (1)
  {
    /* USER CODE END WHILE */

    /* USER CODE BEGIN 3 */

	  control_data.pwm_vref = (4096.0f/3.3f) * (1.563f - 0.0625f*control_data.vCapRef);
	  control_data.vCap = control_data.adc_data_v0*(3.3f/4096.0f)*10.1f  * 1.027;  //1.027 is adjustment factor

	  uint32_t puls_len_pwm = control_data.pulseLen*(3200.0f*20.0f);
	  if(puls_len_pwm > 3200*20*100) puls_len_pwm = 3200*20*100;
	  pulse_data.len = puls_len_pwm;

	  LL_GPIO_SetOutputPin(LED_GPIO_Port, LED_Pin);
	  LL_mDelay(80);
	  LL_GPIO_ResetOutputPin(LED_GPIO_Port, LED_Pin);
	  LL_mDelay(20);

	  float pulsrepcycle = control_data.pulseRep*10.0f;
	  float voltokcycle = control_data.voltok*10.0f;
	  if (pulsrepcycle < 5.0f) pulsrepcycle =  5.0f;    //min 0.5
	  if (pulsrepcycle > 1000.0f) pulsrepcycle = 1000.0f; //max 100s

	  if(control_data.rep_cnt > pulsrepcycle) control_data.rep_cnt = pulsrepcycle;

	  if( (control_data.vCap < (control_data.vCapRef-control_data.vCapTol)) || (control_data.vCap > (control_data.vCapRef+control_data.vCapTol)) ){
		  if(control_data.rep_cnt < voltokcycle){
			  control_data.rep_cnt=voltokcycle;
		  }
	  }

	  if(control_data.rep_cnt > 0){
		  control_data.rep_cnt--;
	  }
	  else{
		  if (control_data.active){
			  pulse_data.start = 1;
			  control_data.rep_cnt = pulsrepcycle;
		  }
	  }

	  char sval[10];
	  itoa(control_data.adc_data_v0, sval, 10); //Base 10 (dec)  //dummy data
	  //itoa(encpos, sval, 16); //Base 16 (hex)
	  //todo leading zeros:
	  //Let itoa() convert
	  //into a temporary buffer, determine the difference between
	  //your target space and strlen(buffer), fill that amount of
	  //zeros into the target space, and then strcpy the buffer
	  //over to target space.

	  uart_printstr(&huart1, sval);
	  uart_printstr(&huart1, "\r\n");

	  //encpos++;
  }
  /* USER CODE END 3 */
}

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


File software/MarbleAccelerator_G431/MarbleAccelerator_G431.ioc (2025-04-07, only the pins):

Mcu.UserName=STM32G431CBUx
PA0.GPIO_Label=VBUS
PA0.Signal=ADC1_IN1
PA1.Signal=OPAMP1_VINP
PA10.GPIO_Label=PWM_3
PA10.Signal=S_TIM1_CH3
PA11.GPIO_Label=CAN_RX
PA11.Signal=FDCAN1_RX
PA12.GPIO_Label=PWM_2N
PA12.Signal=TIM1_CH2N
PA15.GPIO_Label=J3_PWM
PA15.Signal=GPIO_Input
PA3.Signal=OPAMP1_VINM0
PA5.Signal=OPAMP2_VINM0
PA7.Signal=OPAMP2_VINP
PA8.GPIO_Label=PWM_1
PA8.Signal=S_TIM1_CH1
PA9.GPIO_Label=PWM_2
PA9.Signal=S_TIM1_CH2
PB0.Signal=OPAMP3_VINP
PB12.GPIO_Label=POTI
PB12.Signal=ADC1_IN11
PB14.GPIO_Label=TEMP
PB14.Signal=ADC1_IN5
PB15.GPIO_Label=PWM_3N
PB15.Signal=TIM1_CH3N
PB2.Signal=OPAMP3_VINM0
PB3.Signal=USART2_TX
PB4.Signal=USART2_RX
PB6.GPIO_Label=ENC_A
PB6.Signal=GPIO_Input
PB7.GPIO_Label=ENC_B
PB7.Signal=GPIO_Input
PB8-BOOT0.GPIO_Label=ENC_Z
PB8-BOOT0.Signal=GPIO_Input
PB9.GPIO_Label=CAN_TX
PB9.Signal=FDCAN1_TX
PC10.GPIO_Label=BUTTON
PC10.Signal=GPIO_Input
PC11.GPIO_Label=CAN_SHDN
PC11.Signal=GPIO_Output
PC13.GPIO_Label=PWM_1N
PC13.Signal=TIM1_CH1N
PC14-OSC32_IN.GPIO_Label=CAN_TERM
PC14-OSC32_IN.Signal=GPIO_Output
PC6.GPIO_Label=LED
PC6.Signal=GPIO_Output
PF0-OSC_IN.Signal=RCC_OSC_IN
PF1-OSC_OUT.Signal=RCC_OSC_OUT

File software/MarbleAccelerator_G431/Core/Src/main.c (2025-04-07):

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
/* Includes ------------------------------------------------------------------*/
#include "main.h"


FDCAN_HandleTypeDef hfdcan1;

UART_HandleTypeDef huart2;

void SystemClock_Config(void);
static void MX_GPIO_Init(void);
static void MX_OPAMP3_Init(void);
static void MX_OPAMP1_Init(void);
static void MX_OPAMP2_Init(void);
static void MX_TIM1_Init(void);
static void MX_ADC1_Init(void);
static void MX_ADC2_Init(void);
static void MX_FDCAN1_Init(void);
static void MX_USART2_UART_Init(void);
/* USER CODE BEGIN PFP */
extern void FDCAN_Config(void);
extern void control_init(void);
extern void datarec_init(void);
extern int datarec_isNewData(void);
extern void datarec_printResults(UART_HandleTypeDef *huart);
/* USER CODE END PFP */

/**
  * @brief  The application entry point.
  * @retval int
  */
int main(void)
{
  /* MCU Configuration--------------------------------------------------------*/

  /* Reset of all peripherals, Initializes the Flash interface and the Systick. */
  HAL_Init();

  /* Configure the system clock */
  SystemClock_Config();

  /* Initialize all configured peripherals */
  MX_GPIO_Init();
  MX_OPAMP3_Init();
  MX_OPAMP1_Init();
  MX_OPAMP2_Init();
  MX_TIM1_Init();
  MX_ADC1_Init();
  MX_ADC2_Init();
  MX_FDCAN1_Init();
  MX_USART2_UART_Init();
  /* USER CODE BEGIN 2 */

  //Enable Opamps
  LL_OPAMP_Enable(OPAMP1);
  LL_OPAMP_Enable(OPAMP2);
  LL_OPAMP_Enable(OPAMP3);


  //Enable ADCs
  LL_ADC_Enable(ADC1);
  LL_ADC_Enable(ADC2);

  //LL_ADC_EnableIT_EOCS(ADC1);
  //LL_ADC_REG_StartConversionSWStart(ADC1);
  LL_ADC_INJ_StartConversion(ADC1);
  //LL_ADC_EnableIT_EOCS(ADC2);
  //LL_ADC_REG_StartConversionSWStart(ADC2);
  LL_ADC_INJ_StartConversion(ADC2);


  //TIM 4 is for Encoder
  LL_TIM_EnableCounter(TIM4);
  LL_TIM_CC_EnableChannel(TIM4, LL_TIM_CHANNEL_CH3); //Zero marker position


  //TIM1 is for PWM
  LL_TIM_EnableCounter(TIM1);
  LL_TIM_CC_EnableChannel(TIM1, LL_TIM_CHANNEL_CH1);
  LL_TIM_CC_EnableChannel(TIM1, LL_TIM_CHANNEL_CH1N);
  LL_TIM_CC_EnableChannel(TIM1, LL_TIM_CHANNEL_CH2);
  LL_TIM_CC_EnableChannel(TIM1, LL_TIM_CHANNEL_CH2N);
  LL_TIM_CC_EnableChannel(TIM1, LL_TIM_CHANNEL_CH3);
  LL_TIM_CC_EnableChannel(TIM1, LL_TIM_CHANNEL_CH3N);

  //Config / Enable CAN
  //FDCAN_Config();

  control_init();
  datarec_init();

  /* USER CODE END 2 */

  /* Infinite loop */
  /* USER CODE BEGIN WHILE */
  while (1)
  {


    /* USER CODE END WHILE */

    /* USER CODE BEGIN 3 */
	if(datarec_isNewData()){
		datarec_printResults(&huart2);
	}

  }
  /* USER CODE END 3 */
}

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


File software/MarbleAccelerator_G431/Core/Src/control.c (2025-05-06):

/*
  Copyright (c) 2025 Fabian Mink <fabian.mink@gmx.de>
  All rights reserved.

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
  1. Redistributions of source code must retain the above copyright notice, this
     list of conditions and the following disclaimer.
  2. Redistributions in binary form must reproduce the above copyright notice,
     this list of conditions and the following disclaimer in the documentation
     and/or other materials provided with the distribution.

  THIS SOFTWARE IS PROVIDED BY THE COPYRIGHT HOLDERS AND CONTRIBUTORS "AS IS" AND
  ANY EXPRESS OR IMPLIED WARRANTIES, INCLUDING, BUT NOT LIMITED TO, THE IMPLIED
  WARRANTIES OF MERCHANTABILITY AND FITNESS FOR A PARTICULAR PURPOSE ARE
  DISCLAIMED. IN NO EVENT SHALL THE COPYRIGHT OWNER OR CONTRIBUTORS BE LIABLE FOR
  ANY DIRECT, INDIRECT, INCIDENTAL, SPECIAL, EXEMPLARY, OR CONSEQUENTIAL DAMAGES
  (INCLUDING, BUT NOT LIMITED TO, PROCUREMENT OF SUBSTITUTE GOODS OR SERVICES;
  LOSS OF USE, DATA, OR PROFITS; OR BUSINESS INTERRUPTION) HOWEVER CAUSED AND
  ON ANY THEORY OF LIABILITY, WHETHER IN CONTRACT, STRICT LIABILITY, OR TORT
  (INCLUDING NEGLIGENCE OR OTHERWISE) ARISING IN ANY WAY OUT OF THE USE OF THIS
  SOFTWARE, EVEN IF ADVISED OF THE POSSIBILITY OF SUCH DAMAGE.
 */

#include "control.h"
#include "datarec.h"
#define PWM_MAX 2500
#define PWMREF_MAX_CURRENTMEAS    28000    //Max PWM-reference duty cycle, where current measurement is still reliable

//Power stage
static calib_data_t calib_data = {
		.ia = {.offs = 0, .gain = -1900},
		.ib = {.offs = 0, .gain = -1900},
		.ic = {.offs = 0, .gain = -1900},
		.i_autoOffs = true,
		.vbus = {.offs = 47, .gain = 551},
		.poti = {.offs = 0,  .gain = 256},
		.imax = 20 *256,   //20A
		.umin = 8  *256,   //8V
		.umax = 25 *256    //25V
};

//void can_init(void);
//void can_sm(void);

ctrl_data_t myctrl;

typedef enum {
	sens_state_wft = 0,
	sens_state_run = 1, //inside sensor windows
	sens_state_fly = 2, //behind sensor windows, "free flying"
	sens_state_rdy = 3  //in coil
} sensor_states_t;

typedef enum {
	sens_cmd_none = 0,
	sens_cmd_reset = 1,
	sens_cmd_trigger = 2 //for manual triggering
}
sensor_cmd_t;

typedef struct{
	uint32_t cnt;
	uint16_t spd;
	uint32_t pos;
	uint32_t trigpos;
	uint16_t level;
	uint16_t hyst;
	sensor_states_t state;
	sensor_cmd_t cmd;
	int16_t iaref;   //int16, Q7.8
	int16_t ibref;   //int16, Q7.8
	pgenerator_lin_int16_data_t pg_a;
	pgenerator_lin_int16_data_t pg_b;
} sensor_data_t;

sensor_data_t mysensor;
int16_t  pg_a_val[10];
uint32_t pg_a_deltapos[10];
int16_t  pg_b_val[10];
uint32_t pg_b_deltapos[10];

static void pwm_setrefint_3ph_tim1(int16_t ref[3]){
	int i;
	int32_t refi[3];
	uint32_t refu[3];

	for(i=0;i<3;i++){
		refi[i] = ( (int32_t)ref[i]);
		refi[i] += 32768;
		refu[i] = refi[i];
		refu[i] = refu[i] * PWM_MAX;
		refu[i] = refu[i] >> 16;
	}

	TIM1->CCR1 = refu[0];
	TIM1->CCR2 = refu[1];
	TIM1->CCR3 = refu[2];
}

void control_sm_to_ready_mode(void){
	//stop PWM
	LL_TIM_DisableAllOutputs(TIM1); //PWM off
	myctrl.ctrl_sm_cnt = 0;
	myctrl.state = ctrl_sm_state_ready;
	int16_t refs[3] = {0,0,0};
	pwm_setrefint_3ph_tim1(refs);
	//can_init();
}

void control_sm_to_off_mode(void){
	//stop PWM
	LL_TIM_DisableAllOutputs(TIM1); //PWM off
	myctrl.ctrl_sm_cnt = 0;
	myctrl.state = ctrl_sm_state_off;
	int16_t refs[3] = {0,0,0};
	pwm_setrefint_3ph_tim1(refs);
	//can_init();
}

void control_sm_to_error(void){
	//stop PWM
	LL_TIM_DisableAllOutputs(TIM1); //PWM off
	myctrl.ctrl_sm_cnt = 0;
	myctrl.state = ctrl_sm_state_error;
	int16_t refs[3] = {0,0,0};
	pwm_setrefint_3ph_tim1(refs);
}

void control_sm_to_vcon_mode(void){
	myctrl.ua = 0;
	myctrl.ub = 0;
	myctrl.uc = 0;
	myctrl.state = ctrl_sm_state_vcon;
	int16_t refs[3] = {0,0,0};
	pwm_setrefint_3ph_tim1(refs);
	LL_TIM_EnableAllOutputs(TIM1); //PWM on
}

void control_sm_to_ccon_mode(void){
	//Transfer to ccon mode, do initialization of controllers
	myctrl.pi_a.i_val = 0;
#ifndef SINGLECOIL_DESIGN
	myctrl.pi_b.i_val = 0;
#endif
	myctrl.ctrl_sm_cnt = 0;
	myctrl.state = ctrl_sm_state_ccon;
	int16_t refs[3] = {0,0,0};
	pwm_setrefint_3ph_tim1(refs);
	LL_TIM_EnableAllOutputs(TIM1); //PWM on
}

//Control state machine
void control_sm(void){
	if(myctrl.state == ctrl_sm_state_startup){
		myctrl.ctrl_sm_cnt++;
		//delay 0.5s
		if(myctrl.ctrl_sm_cnt >= 8000){
			myctrl.ctrl_sm_cnt = 0;
			myctrl.ia_offs_sum = myctrl.ib_offs_sum = myctrl.ic_offs_sum = 0;
			myctrl.state = ctrl_sm_state_curroffs;
		}
	}
	else if(myctrl.state == ctrl_sm_state_curroffs){
		//wait 0.5s for offset determination
		if(myctrl.ctrl_sm_cnt < 8000){
			myctrl.ctrl_sm_cnt++;
		}
		else {
			if (calib_data.i_autoOffs){
				calib_data.ia.offs = myctrl.ia_offs_sum / 8000;
				calib_data.ib.offs = myctrl.ib_offs_sum / 8000;
				calib_data.ic.offs = myctrl.ic_offs_sum / 8000;
			}
			myctrl.ctrl_sm_cnt = 0;
			control_sm_to_ready_mode();
		}
	}
	else if(myctrl.state == ctrl_sm_state_ready){
		myctrl.ctrl_sm_cnt++;
		//if(myctrl.ctrl_sm_cnt >= 64000){  //with autostart after 4s
		if(myctrl.ctrl_sm_cnt >= 8000){  //with autostart after 0.5s
			//if(button_pressed){
			control_sm_to_ccon_mode();
			//control_sm_to_vcon_mode();
			//}
		}
	}
	else if(myctrl.state == ctrl_sm_state_ccon){
		if(myctrl.cmd == ctrl_sm_cmd_stop){
			myctrl.cmd = ctrl_sm_cmd_none;
			control_sm_to_off_mode();
		}
		else if(myctrl.ctrl_sm_cnt < 8000){ //Switch off via button possible after at least 0.5s
			myctrl.ctrl_sm_cnt++;
		}
		else {
			if(myctrl.button_pressed){
				control_sm_to_off_mode();
			}
		}
	}
	else if(myctrl.state == ctrl_sm_state_off){
		//Restart when button pressed
		if((myctrl.button_pressed) || myctrl.cmd == ctrl_sm_cmd_start){
			myctrl.cmd = ctrl_sm_cmd_none;
			myctrl.ctrl_sm_cnt = 0;
			control_sm_to_ready_mode();
		}
	}
	else if(myctrl.state == ctrl_sm_state_error){
		//Reset via button possible after at least 1s
		if(myctrl.ctrl_sm_cnt < 16000){
			//If button is pressed before 1s elapsed, ignore it and restart counting
			if((myctrl.button_pressed) || myctrl.cmd == ctrl_sm_cmd_start){
				myctrl.cmd = ctrl_sm_cmd_none;
				myctrl.ctrl_sm_cnt = 0;
			}
			else {
				myctrl.ctrl_sm_cnt++;
			}
		}
		else {
			//Error reset when button pressed
			if((myctrl.button_pressed) || myctrl.cmd == ctrl_sm_cmd_start){
				myctrl.cmd = ctrl_sm_cmd_none;
				myctrl.ctrl_sm_cnt = 0;
				control_sm_to_ready_mode();
			}
		}
	}
}
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

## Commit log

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2022-06-15 timing adapted; auto-quit errors
    [main.c]
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2023-04-18 16kHz PWM corrected and verified
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2025-03-12 cad files added
    [base.FCStd, ring.stl, tube.FCStd]
2025-03-15 FEMM and result evaluation updated; data fitting to parametric function
    [output_Ia_z.csv]
2025-03-15 geometry optimized
    [tube.FCStd]
2025-03-15 winding assistant added stl files added
    [tube-Body.stl, tube.FCStd, winding_assistant-Body.stl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]
2025-03-17 nominal pocket size increased due to printing tolerances
    [winding_assistant-Body.stl, winding_assistant.FCStd]
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2025-03-20 re-calculation / simulation for 0.5mm wire diameter
    [output_Ia_z.csv]
2025-03-21 new "vertical" design (not tested yet)
    [base-Body.stl, base.FCStd]
2025-03-21 runway holder improved
    [base-Body.stl, base.FCStd]
2025-03-22 height corrected, sensor hole stop added, wire holes added
    [base-Body.stl, base.FCStd]
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2025-03-24 velocity equation improved: index does not work for "dotted" variable in github
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2025-03-24 code rework and cleanup
    [control.c, control.h, main.c]
2025-03-24 0.5mm Ramp added to runway
    [base-Body.stl, base.FCStd]
2025-03-25 height adjusted; bottom hole for coil winding machine fixation; detector hole optimized
    [base-Body.stl, base.FCStd]
2025-03-25 winding assistant added
    [windingAssistant-Body.stl, windingAssistant.FCStd]
2025-03-26 Mounting holes added
    [base-Body.stl, base.FCStd]
2025-03-26 horizontal design files moved to subfolder
    [base-Body.stl, base.FCStd, tube-Body.stl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]
2025-03-26 output tube added
    [outputTube-Body.stl, outputTube.FCStd]
2025-03-26 output for vertical coil optimized
    [base.FCStd, outputTube-Body.stl, outputTube.FCStd]
2025-03-26 timing corrected (max PWM values); code cleanup an rework
    [MarbleAccelerator_G431.ioc, control.c, main.c]
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2025-03-29 current setpoint generation moved to sensor_calculation; output voltage calculation corrected
    [control.c]
2025-03-29 hole diameter increase to 10mm due to winding machine shaft diameter
    [winding_assistant-Body.stl, winding_assistant.FCStd]
2025-03-30 magnetics model functions optimized
    [output_N180.csv]
2025-03-31 brackets added correctly
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2025-04-06 fem calculation for variation of both ia and ib
    [output_Ia_Ib_z.csv]
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2025-04-11 tech drawings improved / updated
    [base.FCStd]
2025-04-11 hight dimension added to techdraw
    [base.FCStd]
2025-04-11 cable output added
    [base-Body.stl, base.FCStd]
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2025-04-14 wrong current measurement phase b workaround
    [control.c]
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2025-04-14 wrong references corrected, parameters tuned; now working for single coil design
    [control.c]
2025-04-14 shorter wait time for next marble
    [control.c]
2025-05-06 additional holes for coil wire
    [tube-Body.stl, tube.FCStd]
2025-05-13 controller baseplate added
    [baseplate.FCStd]
2025-05-13 connectors + holders
    [baseplate-Body.stl, baseplate.FCStd]
2025-05-13 tech draw added
    [base.FCStd]
2025-05-13 holder for stepup converter removed; clamp rails added
    [baseplate-Body.stl, baseplate.FCStd]
2025-05-15 mount for wago cage clamp
    [baseplate-Body.stl, baseplate.FCStd]
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2026-01-27 extensionTube added
    [extensionTube-Body.stl, extensionTube.FCStd]
2026-01-27 variable height; 70mm varian stl added
    [extensionTube.FCStd, extensionTube_70mm-Body.stl]
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2026-02-08 boost converter KiCAD project added
    [boost_converter.kicad_pcb, boost_converter.kicad_sch]
2026-02-10 silk screen optimized; drc ok
    [boost_converter.kicad_pcb]
2026-02-10 Labels added; ready for production
    [boost_converter.kicad_pcb]
2026-02-11 board carrier for electronics added
    [board_carrier.FCStd]
2026-02-12 hi side switch pcb draft added
    [hiside_switch.kicad_pcb, hiside_switch.kicad_sch]
2026-02-14 routing completed
    [hiside_switch.kicad_pcb, hiside_switch.kicad_sch]
2026-02-14 hiside switch added
    [board_carrier.FCStd]
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2026-02-14 hi side switch board mounting and controller board pad added
    [board_carrier.FCStd]
2026-02-16 sketch and hole naming
    [base.FCStd]
2026-02-16 output catcher added
    [outputCatcher.FCStd]
2026-02-16 tower added
    [trussTower.FCStd]
2026-02-16 tower completed; pin added
    [Pin.FCStd, trussTower.FCStd]
2026-02-16 stls added
    [Pin-Body.stl, outputCatcher-Body.stl, trussTower-Body.stl]
2026-02-17 height parametrized
    [trussTower.FCStd]
2026-02-17 fixation pin diameter corrected; stl updated
    [trussTower-Body.stl, trussTower.FCStd]
2026-02-17 mounting hole diameter increased to 3.2mm
    [outputCatcher-Body.stl, outputCatcher.FCStd]
2026-02-18 height increased; inlet hole on all sides
    [trussTower-Body.stl, trussTower.FCStd]
2026-02-18 Mounting hole size increased from 3.0mm to 3.2mm; wire hole position optimized
    [base-Body.stl, base.FCStd]
2026-02-19 Stability optimized
    [trussTower-Body.stl, trussTower.FCStd]
2026-02-21 Fixation hole Diameter and Depth increased
    [trussTower-Body.stl, trussTower.FCStd]
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2026-02-24 USB connector pocket optimized
    [board_carrier.FCStd]
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2026-04-15 drawing name changed; pdf export
    [base.FCStd]
2026-04-15 runway path inclination increased
    [base-Body.stl, base.FCStd]
2026-04-15 "open" variant for vertical accelerator added
    [base_open.FCStd, base_open_base-Body.stl, base_open_base.FCStd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]
2026-04-16 coil runway removed; additional coil without top
    [base_open_coil-Body.stl, base_open_coil.FCStd, base_open_coil_noTop-Body.stl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]
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2026-04-19 resolution reduced, individual filename
    [point_output_-15mm_10A.csv, point_output_-15mm_20A.csv]
2026-04-22 housing for hi-side switch board only added
    [board_carrier_SwitchOnly.FCStd]
2026-04-24 TechDraw / 3D View added
    [board_carrier_SwitchOnly.FCStd]
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2026-04-27 outer dimensions adjusted für Auer eurobox
    [Baseplate-BodySketch_Baseplate.dxf, Baseplate.FCStd]
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2026-05-04 Baseplate with variable cell diameter added (e.g. for tuning to laser beam width)
    [Baseplate_35cmx25cm_variableCell.FCStd]
2026-05-19 Version for steel filling added
    [outputCatcherFilled.FCStd]
2026-05-20 Top of filling pocket optimized
    [outputCatcherFilled.FCStd]
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2026-05-22 stick length decreased by 1mm
    [trussTower-Body.stl, trussTower.FCStd]
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2026-06-03 final optimal cell width 29.5mm
    [Baseplate_35cmx25cm-BodySketch_Baseplate.dxf, Baseplate_35cmx25cm.FCStd, Baseplate_35cmx25cm_variableCell.FCStd]

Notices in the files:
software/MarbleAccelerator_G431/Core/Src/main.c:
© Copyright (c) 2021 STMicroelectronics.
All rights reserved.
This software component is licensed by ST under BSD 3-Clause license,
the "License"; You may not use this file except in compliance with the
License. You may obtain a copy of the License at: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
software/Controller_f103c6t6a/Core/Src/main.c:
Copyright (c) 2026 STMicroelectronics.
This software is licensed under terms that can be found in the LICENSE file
